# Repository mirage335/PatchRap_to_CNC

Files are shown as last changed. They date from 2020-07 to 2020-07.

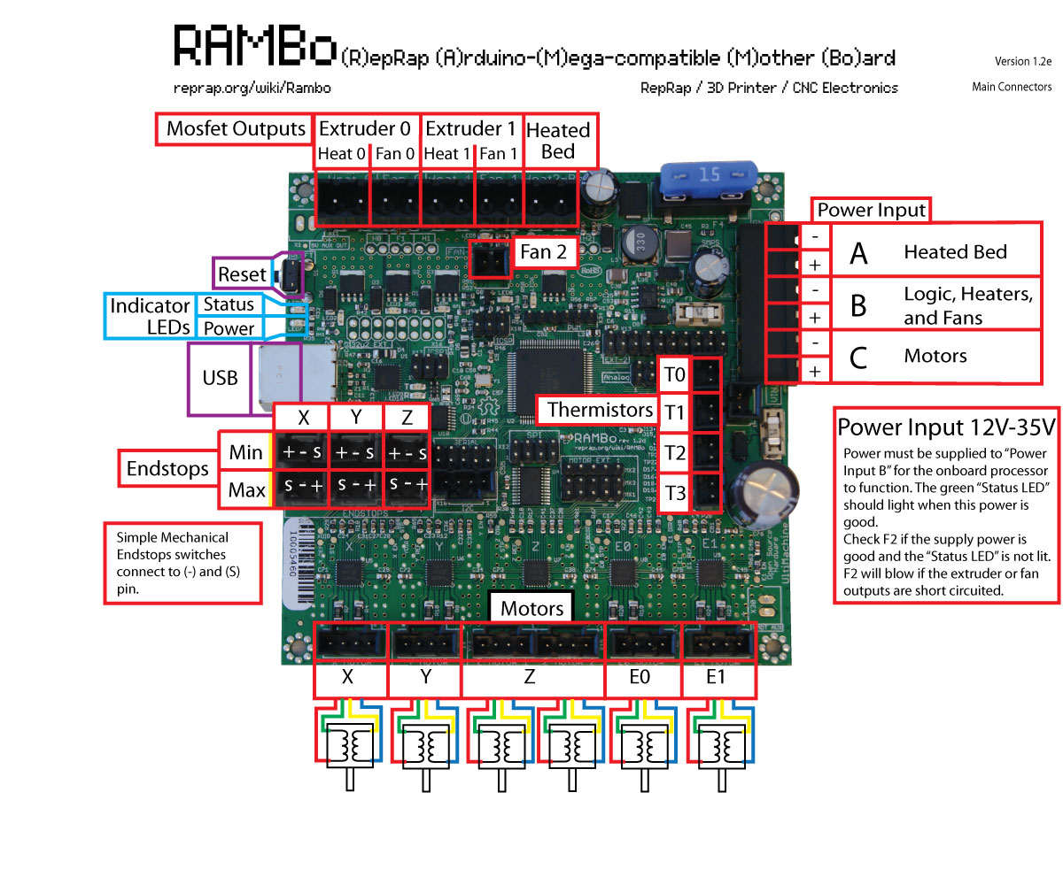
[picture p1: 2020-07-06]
_out_PatchRap_symbols/_ref/diagrams/rambo/v1.3_Rambo1-2-conn-main.jpg

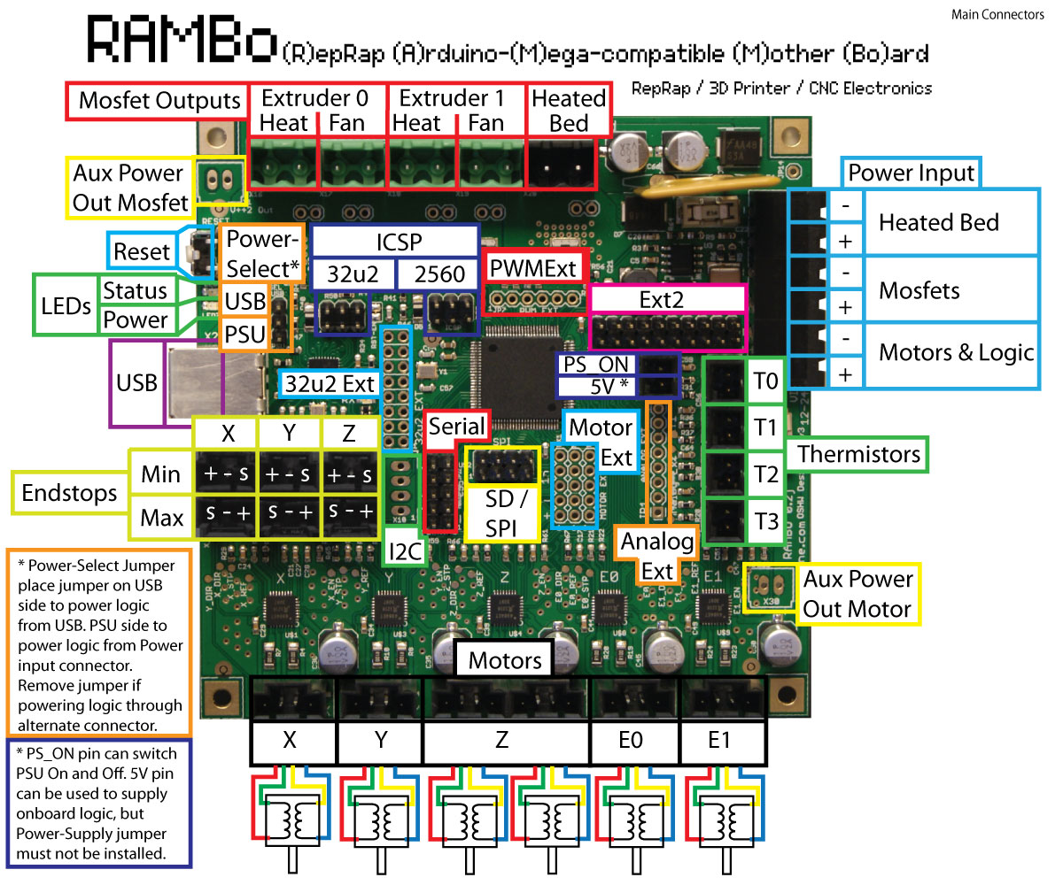
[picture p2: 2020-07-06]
_out_PatchRap_symbols/_ref/diagrams/rambo/v1.0-v1.1_Rambo-conn-all.jpg

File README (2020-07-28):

Copyright (C) 2020 mirage335
See the end of the file for license conditions.
See license.txt for PatchRap_to_CNC license conditions.

Compact adapters for CNC machines, converting PatchRap standards to other connectors, including solderable wire-to-board.

__Usage__

Beware that in practice, the generic PatchRap patches are at least as versatile, being breadboard friendly. Specialized adapters may be only rarely justified.

___ PatchRap_to_CNC__WiringDiagram_GenericRap ___

Typically intended to serve as a wiring diagram. Standard solid-core copper Cat5E or similar 'Ethernet' wire can typically plug into a breadboard directly.

Alternatively, may be used as a flexible PCB layout, with breakaway header sockets installed where appropriate.

Beware, some extruders may draw enough current from the 'heater' wires to require multiple connections to the breadboard.

__Design__

WARNING: Correct color coding requires launching PCB with correct color coding parameters, such as with the '_pcb_color_T568A' script provided by "gEDA_designer" . From there, the diagram may be used interactively with 'f' and 'Shift + f' keybindings, or exported to PNG from the PCB program.

WARNING: PCB 'exclude' layers may be used to document connections within components. These possible distractions should be omitted from fabricated PCBs, printed wiring diagrams, mechanical assembly guides, and similar.

USA companies provide all parts in these schematics.

__Safety__
Contrary to typical RAMBo motherboard expectations, Vsys directly from PSU is used for Hotend power, and may be unfused.

LulzBot Mini, Taz5, and similar, connectors, must be tested to adhere to specified Hotend Heater polarity. Reverse connection may present unfused (all RAMBo motherboard fuses bypassed) short-circuit load exceeding 20A, severely overloading MOSFET, wiring, and connectors.

Consider adding fiberglass or silica high-temperature sleeving to wiring near hotend.

__Reference__
https://www.mouser.com/Semiconductors/Discrete-Semiconductors/Diodes-Rectifiers/_/N-ax1ma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|0

https://en.wikipedia.org/wiki/Point-to-point_construction

https://www.mcmaster.com/high-temperature-sleeving/
https://www.mcmaster.com/high-temperature-sleeving/fiberglass-high-temperature-sleeving/
https://www.mcmaster.com/high-temperature-sleeving/expandable-electrical-insulating-tube-sleeving/
https://e3d-online.com/products/fibreglass-sleeving-for-insulating-thermistors-100mm
https://www.mcmaster.com/high-temperature-sleeving/silica-high-temperature-sleeving/

__Copyright__
This file is part of PatchRap_to_CNC.

PatchRap_to_CNC is free software: you can redistribute it and/or modify
it under the terms of the GNU General Public License as published by
the Free Software Foundation, either version 3 of the License, or
(at your option) any later version.

PatchRap_to_CNC is distributed in the hope that it will be useful,
but WITHOUT ANY WARRANTY; without even the implied warranty of
MERCHANTABILITY or FITNESS FOR A PARTICULAR PURPOSE.  See the
GNU General Public License for more details.

You should have received a copy of the GNU General Public License
along with PatchRap_to_CNC.  If not, see <http://www.gnu.org/licenses/>.

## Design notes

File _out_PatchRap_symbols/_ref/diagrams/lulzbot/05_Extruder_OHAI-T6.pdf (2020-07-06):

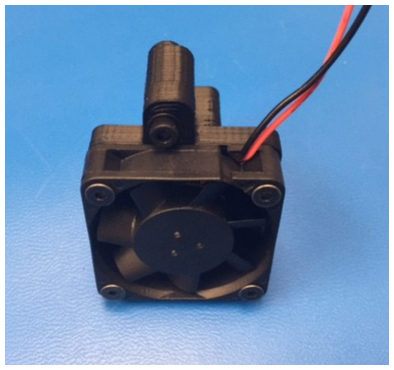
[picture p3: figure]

### Taz 6- Nutmeg Generation Extruder Assembly

10) Prep sub-assemlies

Utiltize OHAI for Hexagon Hot End to build a .5mm Hot End Assembly

Utilize OHAI for Extruder Body sub-assembly to build a Extruder Body assembly (Herringbone gears will be Green).

20) Attach X end stop switch to the Fan Duct, RIGHT (PP-GP0212). Note the Orientation of the switch, this is critical. Tighten screws to 3 in-lbs (~.35N-m) Use:
2x- M2 x 6 SHCS
2x- M2 SS washer
30) Prepare the Hexagon heat sink fan and attach to the Hexagon Hot End Heat Sink fan duct (PP-GP0232 ) with inserts already installed. Note orientation of fan. Use: 4x- M3x 12 SHCS tighten to 8 in-lbs (~.9N-m)

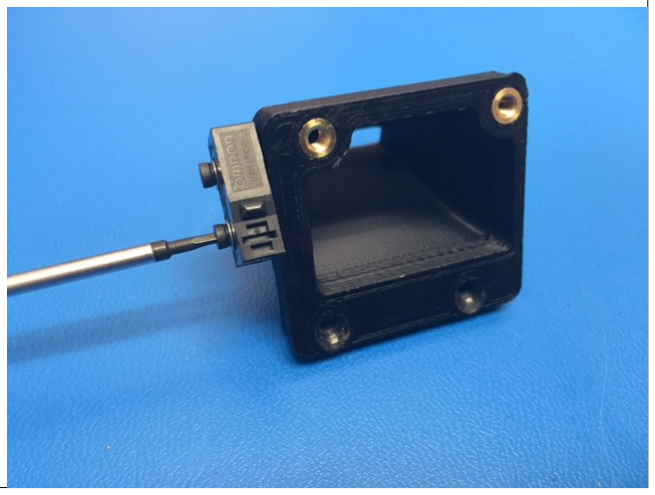
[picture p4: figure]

40) Plugging Order for the devices to be connected to a 16 pin Molex connector

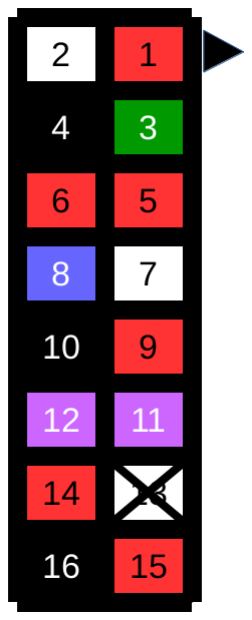
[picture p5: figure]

1- Red- Motor
2- White- Motor
3- Green- Motor
4- Black- Motor
5- Red- Heater Cartridge
6- Red- Heater Cartridge
7- White- Dual fan
8- Blue- Dual Fan
9- Red- Heat Sink Fan
10- Black- Heat Sink Fan
11- Purple- Switch
12- Purple- Switch
13- Empty
14- Red- Ground Wire
15- Red- Thermistor
16- Black- Thermistor

50) Attach the Hot End Assembly to the Dual fan extruder mount v0.5

Utilize OHAI for Hexagon Hot End .5mm assembly
Use:
1x- Extruder Mount TAZ6 (PP-GP0208)
1x- .5mm Hexagon Hot End assembly
1x- Extruder body assembly (PP-GP0186) 1x- Hot End adapter plate
2x- M3x 12 SHCS
2x- M3 nut SS

Connect the Heater Cartridge and Thermistor to the 16 pin connector attached to the motor

60) Connect the Hexagon Hot End ground wire (220mm long) to the hot end. Route the ground wire behind the hot end, Plug ground wire into the 16pin connector that is attached to the motor.

Use:
1x- 4-40 BHCS SS
1x- 4-40 star washer
70) Attach the Left (PP-GP0211) and Right (PP-GP0212) fan ducts to the Extruder Mount TAZ6

Use:
2x- M3 x 12 FHS (for each duct), tighten to 8 in-lbs (~.9 N-m)

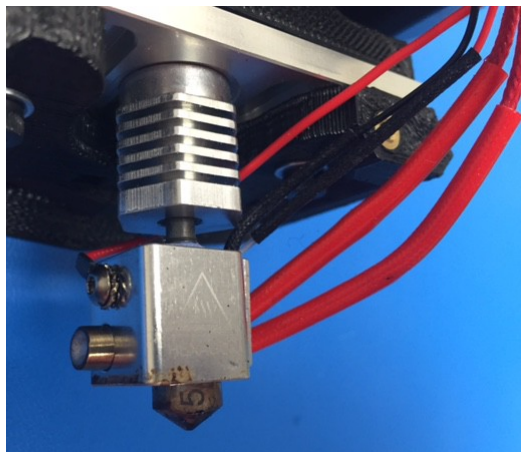
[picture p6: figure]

80) Prepare the Hexagon hot end dual fan sub-assembly

Layout the assembly in front of the Extruder with the fan that has the longest wire cut length to the left of the extruder and the shortest to the right side of the extruder.

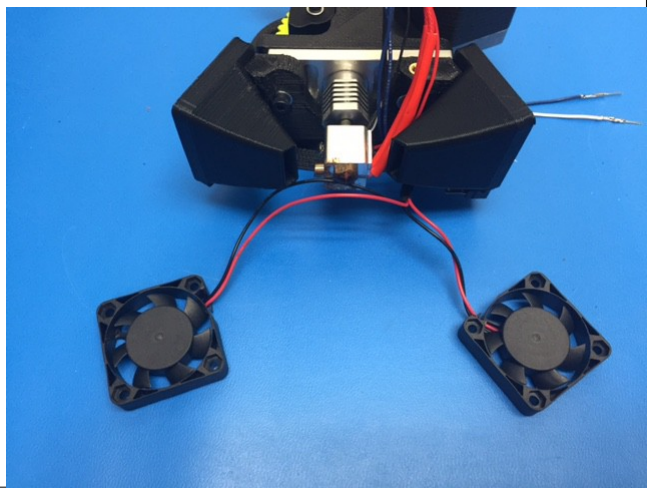
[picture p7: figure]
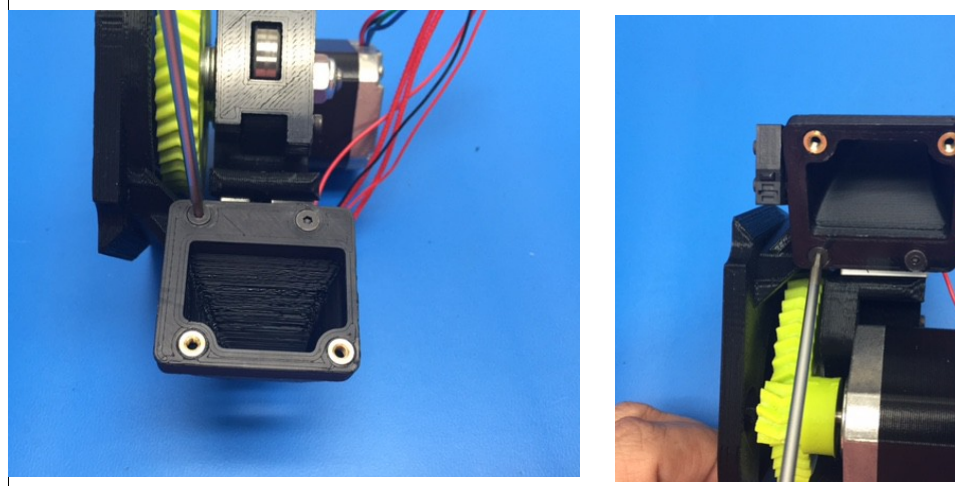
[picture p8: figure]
Left; Right
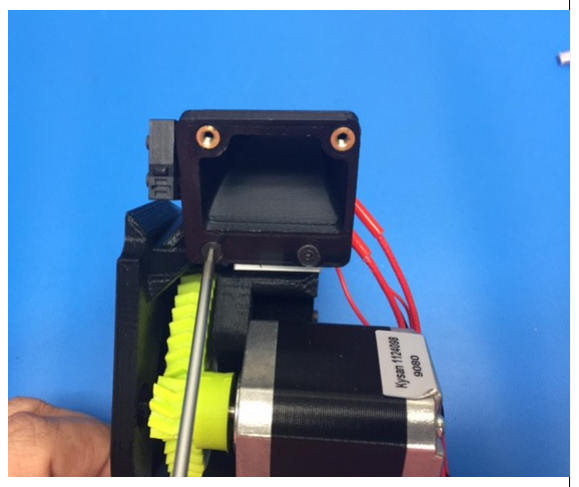
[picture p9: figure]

100) Attach the short fan to the Duct, Right. Note Orientation of the wires exiting the fan.
Use: 2x- M3x 12 SHCS; tighten to 8 in-lbs (~.9 N-m)
90) Attach the long fan to the Duct, Left. Note Orientation of the wires exiting the fan.
Use: 2x- M3x 12 SHCS; tighten to 8 in-lbs (~.9 N-m)

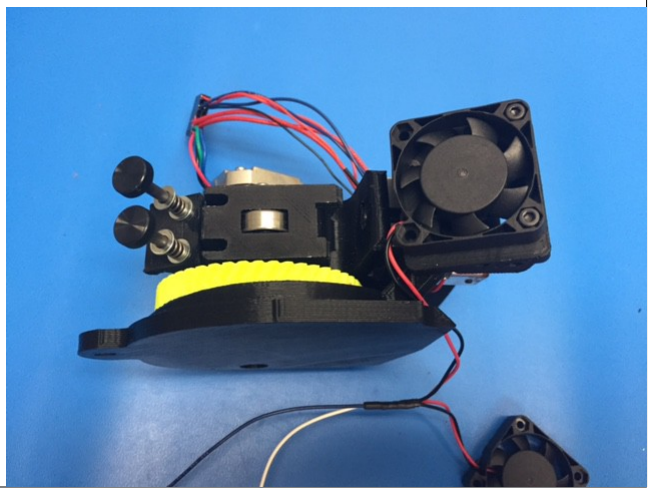
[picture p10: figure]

110) Route the long fan wire along the back of the mount, secure in place with a Ty wrap as shown, proper routing is critical

Connect the Heater Cartridge and Thermistor to the 16 pin connector attached to the motor

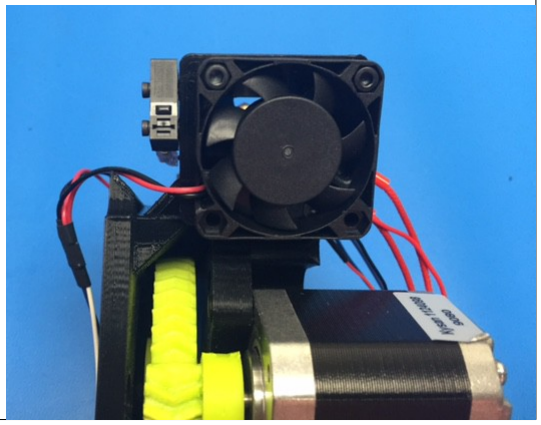
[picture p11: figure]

120) Connect Switch to the 16 pin connector, connect to the switch terminals shown; route wires as shown
Use:
2x- 190mm Blue wire with terminals and Faston PIDGN connector

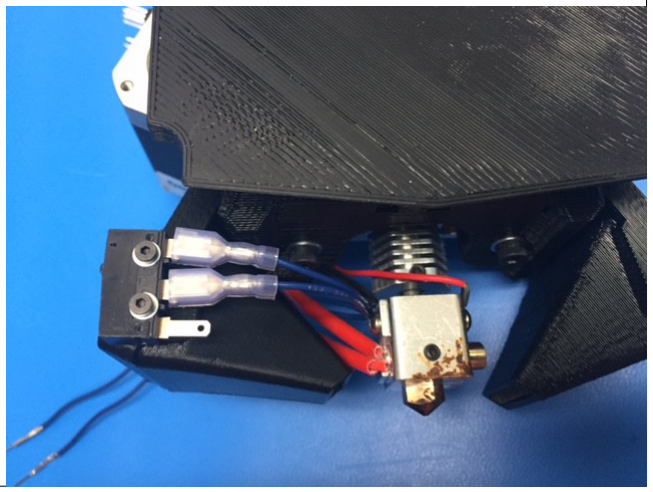
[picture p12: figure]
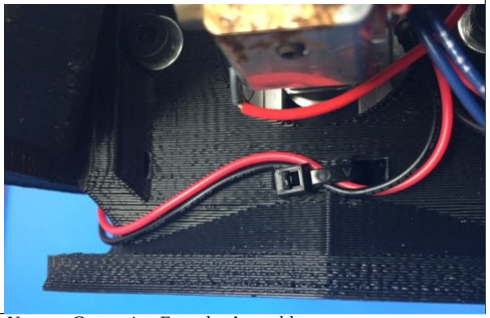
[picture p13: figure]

130) Attach Heat Sink Fan Duct to assembly
Route wires into the duct channel as shown, secure duct to assembly Use:
1x- M3x 25 SHCS; 1x- M3 washer; ; tighten to 8 in-lbs (~.9 N-m)
140) Attach Heat Sink fan to 16 position connector
Wrap 3/4” panduit (110mm length) around wires starting at the bottom of the connector and completing as far down the wire bundle as possible
Secure the panduit to the wire bundle with one Ty Wrap; Position the Ty Wrap approximately where shown

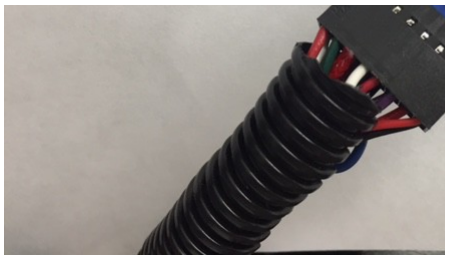
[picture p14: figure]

### 150) Apply the Connect Up label onto the Pin 1 side of the connector nearest the pins extending from the connector

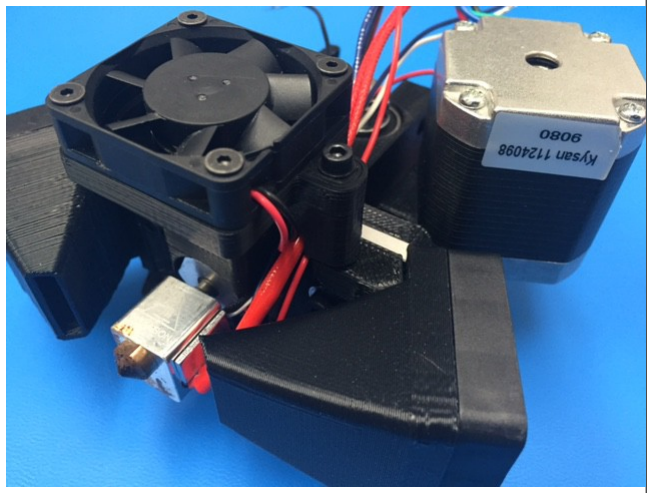
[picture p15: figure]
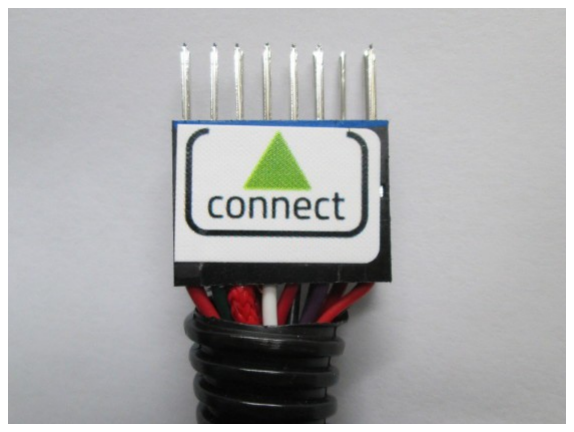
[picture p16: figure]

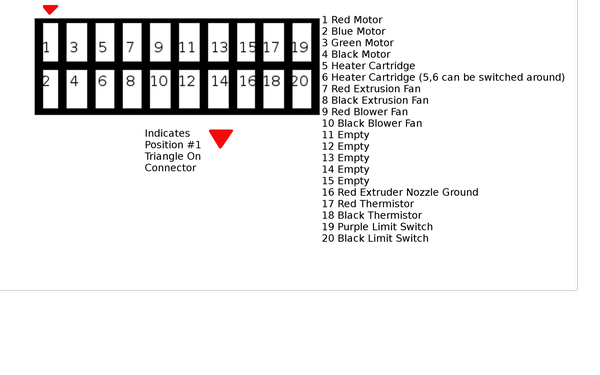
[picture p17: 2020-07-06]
_out_PatchRap_symbols/_ref/diagrams/lulzbot/Wire_Diagram_1.png.600x0_q85.png

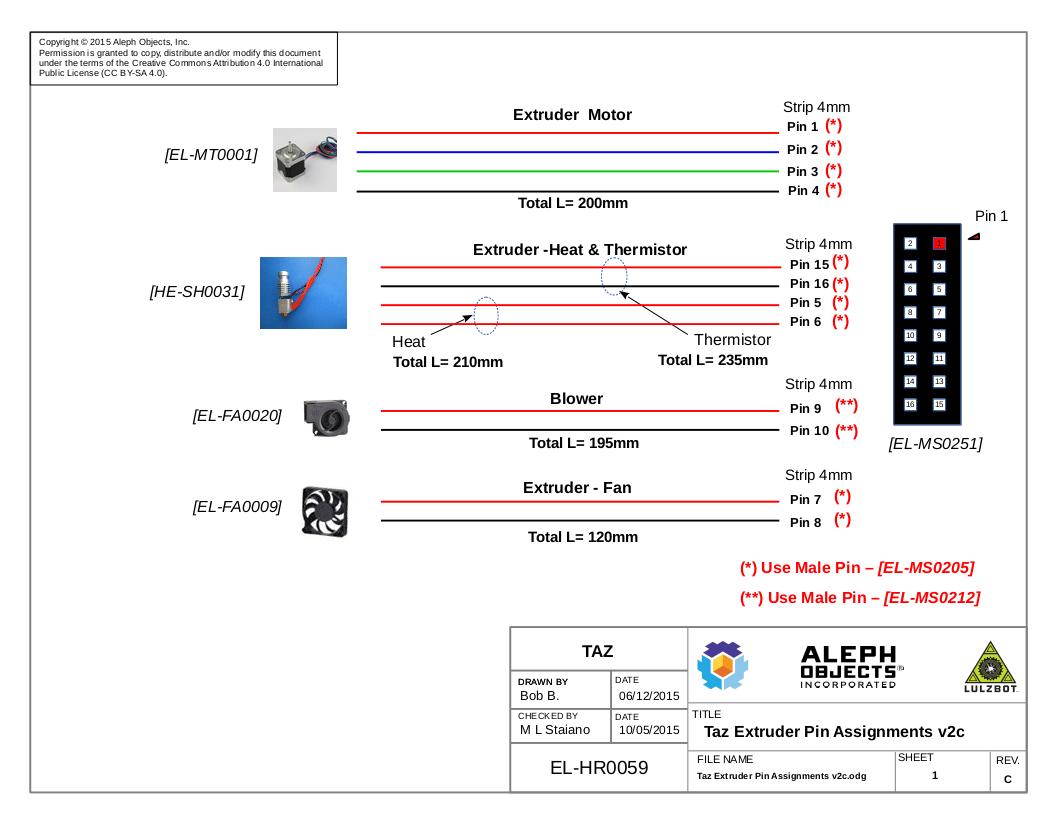
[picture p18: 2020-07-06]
_out_PatchRap_symbols/_ref/diagrams/lulzbot/Taz Extruder Pin Assignments v2c.jpg

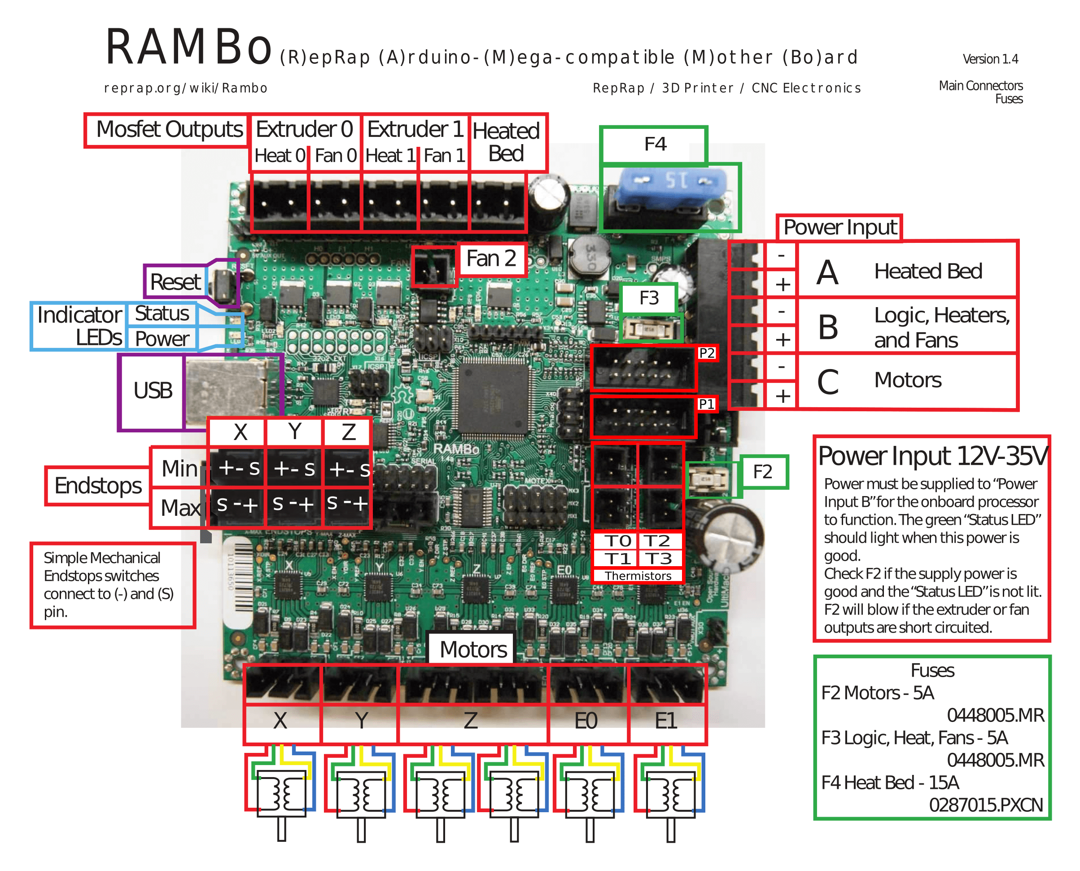
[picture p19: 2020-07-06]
_out_PatchRap_symbols/_ref/diagrams/rambo/v1.4_Rambo-1.4-connection-diagram.png

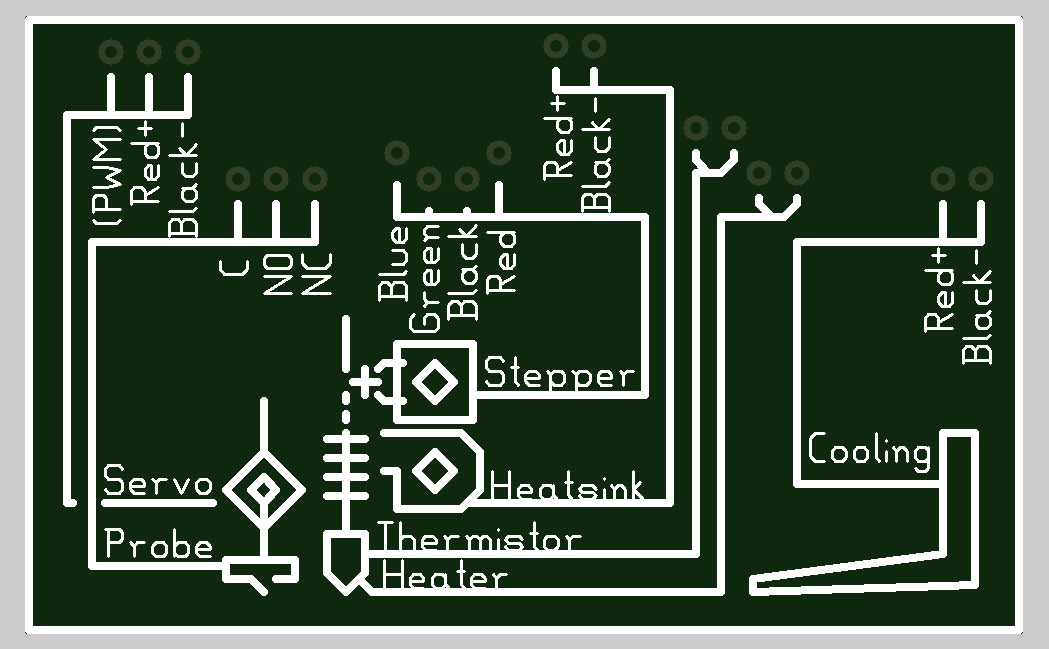
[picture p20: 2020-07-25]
_out_PatchRap_symbols/footprints/illustration_extruder_typical_RenderTop.png

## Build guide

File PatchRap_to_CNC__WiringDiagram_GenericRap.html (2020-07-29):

refdes | device | value | footprint | description | qty | cost | Mouser Part
(M1) | GenericRap | unknown | _M1__GenericRap_WireShield | DISTRIBUTOR NOT YET KNOWN | 1
(M2) | GenericRap_Cutdown | unknown | _M2__GenericRap_Cutdown | DISTRIBUTOR NOT YET KNOWN | 1
(M3) | GenericRap_Cutdown | unknown | _M3__GenericRap_Cutdown_WireShield | DISTRIBUTOR NOT YET KNOWN | 1
(I1) | unknown | unknown | breadboard | unknown | 1
(D1|D2) | DIODE | 0.4V | DIODE_LAY 600 | $0.26 MOUSER 750-CDBU0530 | 2 | $0.26 | 750-CDBU0530
(C1|C2) | CAPACITOR | 1n | ACY400P | $0.72 MOUSER 80-C0402C102F5GECTU | 2 | $0.72 | 80-C0402C102F5GECTU
(I2) | unknown | unknown | illustration_extruder_typical | unknown | 1
(BRK1|BRK2|BRK3) | CONNECTOR_6 | - | JUMPER6 | $0.21 MOUSER 571-6404556 | 3 | $0.21 | 571-6404556

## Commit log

2020-07-08 Breakaway connector placement.
2020-07-29 Illustrate optional double socket connection to breadboard for higher power heater.
2020-08-29 Legacy jumper wiring brought into compliance with PatchRap_LulzBot project.
    [PatchRap_to_CNC.sch, PatchRap_to_CNC__WiringDiagram_GenericRap.sch]
2020-09-17 Documentation. Soldermask clearance around breadboard rail connection vias.
2020-09-28 Correct stepper motor wiring standard.
    [PatchRap_to_CNC__WiringDiagram_GenericRap.sch]
